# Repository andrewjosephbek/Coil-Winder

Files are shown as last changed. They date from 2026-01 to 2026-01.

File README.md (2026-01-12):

# Coil Winder

A **low-cost, precision coil winding machine** built from 3D-printed parts and off-the-shelf components, designed for sensing coils, charging coils, solenoids, and similar applications. See detailed system descriptions and methodology in **Design Docs**. 




---

## Highlights
- Winds coils up to **30 mm length × 250 mm diameter**
- Single-piece **3D-printed frame** for tight tolerances and fast assembly
- **Arbor + Eye architecture** for accurate wire placement
- **Stepper-driven arbor** with 3:1 belt reduction for consistent tension
- **Worm-gear driven eye (40:1)** for fine linear positioning
- Custom **4-layer driver PCB** (STM32L432 + DRV8825)
- **FreeRTOS-based firmware** with prioritized motor control and UI tasking

---

## System Overview
- **Arbor Assembly:** Rotates the coil form and maintains wire tension  
- **Eye Assembly:** Precisely guides wire placement across the arbor  
- **Driver Board:** Handles UI, motor drivers, and peripherals  

---

## Tech Stack
STM32L432 · DRV8825 · FreeRTOS · Step/Dir Steppers · 4-layer PCB · 3D Printing

---

## Capabilities
- Tightly packed first-layer winding
- Supports **30 AWG wire**
- Integrated button-based user interface

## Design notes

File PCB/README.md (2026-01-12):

# coilwinder PCB

[Replace these texts and sections as needed.  This file should desribe the PCB, and associated information.]

## Background

[Fill this out with general info]

## [Next Section]

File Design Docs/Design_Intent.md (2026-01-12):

# Design Intent

This document is a high level overview of the design and structure of this project.

## Project Structure

This project intends to provide a simple and cost effective way to wind coils, using 3D printed and off the shelf components. It's maximum coil size of 30mm Lg x ⌀250mm makes this project well suited for sensing coils, charging coils, solenoids, and similar applications. At the highest possible level, this project is split into two mechanical assemblies, and one electrical assembly. These assemblies are described below:

- The Arbor is the form on which the coil is wound. It's driven by the *Arbor Motor Assembly*.
- The Eye sets the position of the wire relative to the arbor. It's driven by the *Eye Motor Assembly*.
- The *Driver Board* manages and controls the user interface, motors, and other peripherals.

## Mechanical Component Structure

The mechanical side of this project is built on a single part, 3D printed frame. By printing the frame as a single part, tight position tolerances can be met without the need for measuring and positioning components by hand. It also saves on assembly time. 

### Arbor Motor Assembly

The Arbor Motor Assembly is comprised mainly of a stepper motor with a 3:1 timing pulley gear reduction. This provides the necessary torque to maintain tension on the wire while the coil is wound. The Arbor itself is 3D printed and parametric, so that it may be scaled to accommodate a variety of coil sizes. It includes a wire retention screw to keep the wire tight wile the first coil is being wound, as well as coil tie off slots that allow the user to mechanically support the coil before it's removed from the Arbor.

### Eye Motor Assembly

The Eye Motor Assembly uses a 40:1 worm gear reduction to accurately position the eye relative to the Arbor. When the coil winding process starts, the Eye first finds an initial reference angle using a limit switch. It uses this reference angle alongside some computation to determine it's linear position from it's angular position. This method of extracting linear motion from angular motion was chosen since it provides very fine positional resolution and uses fewer parts then a traditional linear rail and lead screw system.

## Control Flow

This project is divided into two tasks (or "threads"), with control flow managed via FreeRTOS. The UI Task (which manages the User Interface) is of Normal OS priority. When the user begins the coil winding process, the UI Task Resumes the execution of the Motor Task. Since the Motor Task is of Above Average OS priority, it takes priority in execution, and only relinquishes control once the coil winder process concludes. This is done intentionally, as an extended interruption in execution may cause the arbor to lose tension on the wire being would, creating a defect in the coil. The UI and Motor Tasks are described below:

### UI Task

The UI task receives user input and updates the User Interface accordingly. The UI Task manages manages the followings sup-processes in the order described below.

#### Setup

1. Initializes the display where the UI is printed
2. Prints the user interface

#### Loop

1. Polls input from the user
2. Set's the position of the user's cursor
3. Updates the value (stored in memory) of the field the user is currently editing
4. Updates the value of the field displayed on the screen from the value stored in memory
5. Chooses to allows the Motor Task to begin execution.

### Motor Task

The Motor Task operates the coil winding process. The Motor Task manages manages the followings sub-processes in the order described below.

#### Setup
1. Initializes and enables stepper motor drivers
2. Suspends the Motor Task

#### Loop
1. Guides the user through the coil winding process through on screen prompts
2. Calculates the required steps to move the Eye at distances specified during the UI Task, and executes those steps. Calculates the required delay to move the Arbor at a consistent speed with respect to it's diameter, and executes those steps
3. Sleeps and disables the stepper motor drivers
4. Reminds the UI Task to redraw it's UI when the coil winding process has concluded
5. Suspends the Motor Task

## Code Structure

The two main tasks call a set of libraries that keep the data they manage organized and the code they run on dry. Each library defines an object that stores data about the component the library is meant to represent. These libraries and their interactions are described in the flow chart and object descriptions below:

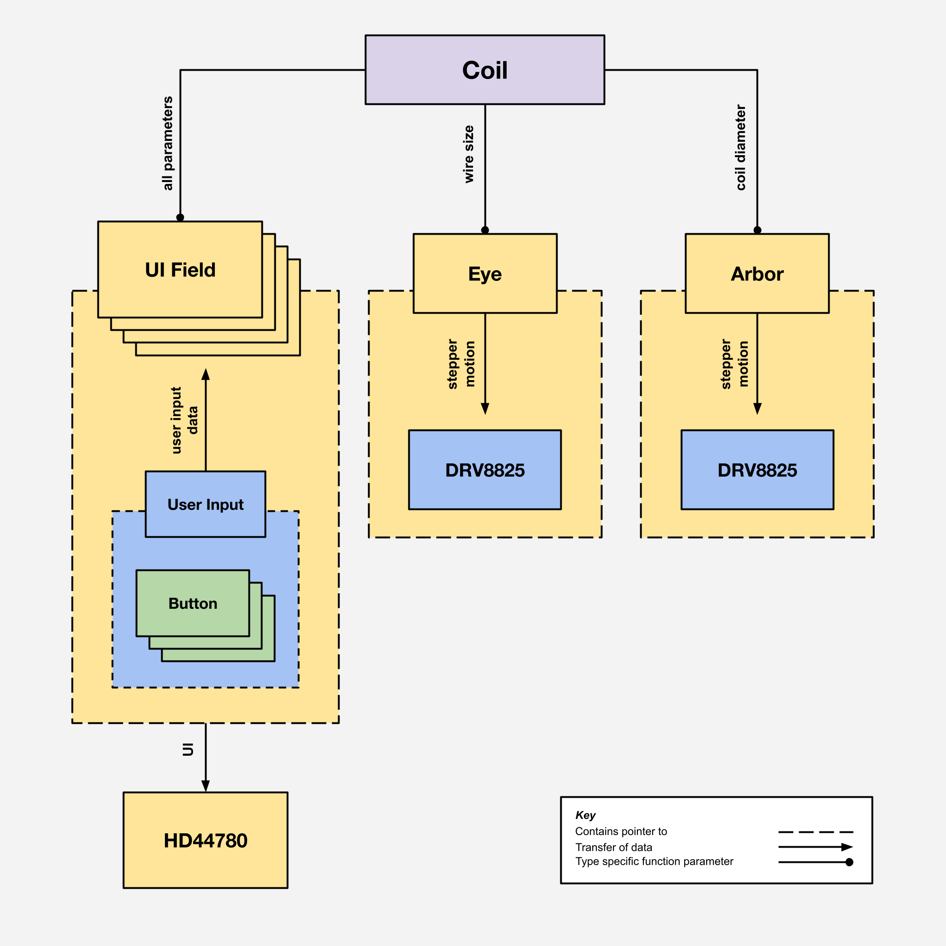
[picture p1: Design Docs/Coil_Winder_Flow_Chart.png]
Flow Chart Title


- `CoilParameters_t` an object that stores the dimensions of the coil to be wound. It's corresponding library can be used to access and change these dimensions.
- `Button_t` an object that stores the GPIO interface and state of a button. This information is used in the Button object's corresponding library to support features like customizable press and hold behaviors, as well as normally open and normally closed switch types.
- `ArborParameters_t` an object that stores the Arbors surface speed and a pointer to it's corresponding . It's corresponding library can be used to rotate the Arbor, and set it's surface speed automatically based on the size of the coil being used.
- `DRV8825_Stepper_t` an object that stores GPIO information about a DRV8825_Stepper_t stepper driver chip. IIt's corresponding library provides low level control of most of the chips functions. 
- `EyeParameters_t` an object that stores the position, length, and DRV8825_Stepper_t for the Eye. It's corresponding library can be used to find it's home position or move the a predetermined distance 
- `UserInput_t` an object that can be used to retrieve user input as a single 32 bit value. It polls it's associated Button_t objects and aggregates their outputs into a single enumeration.
    - It's important to poll user input *only once per tick*. Otherwise, some statements executed in the same tick may see different user input values.
- `UIField_t` an object that stores the title and data accessor functions for a UI field. It's corresponding library can be used to print and update the UI field.

## Driver Board Component Choices

The Driver Board is a 4 layer PCB that serves to drive the display and stepper motors. The components utilized and justifications for their usage are described below.

- The ***STM32L432KCU6*** was chosen as this projects MCU for it's low cost, low power draw, and appropriate number of GPIO ports. 
- The ***DRV8825*** was chosen to drive this projects stepper motors for it's simple step and direction interface. It's current setting potentiometer also negates the need for a SPI current setting and interface, which saves on the number of required MCU GPIO ports.
- The ***AZ1117C*** was chosen for LCD and MCU voltage regulation, as it comes preset at 5V and 3.3V levels, which lowers the number of supporting components required on the PCB.

All other components are standard/trivial supporting components chosen for easy hand-soldering assembly. All SMD resistors and capacitors are package size 0603 (Imperial).

## Current Issues

Though this project currently works as intended, some issues must be addresses before it is developed further:

- Motor task currently performs some limited display functions
    - Would require Motor Task to relinquish control during execution, and for more data to be shared between tasks
- GPIO ports won't Read/Write without first being driven from incorrect port on line 615.

## Planned Updates

In it's current state, this project is in the process of transitioning from working prototype and a first product iteration. In the future, I hope to:

- Transition to a 2 layer PCB, to save on cost
- Design an enclosure to house the display and driver electronics
- Transition to USB as the projects primary power source

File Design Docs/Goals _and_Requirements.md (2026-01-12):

# Goals and Requirements

Requirements describe features that must be implemented, goals are features that may be added once a minimum viable product is achieved.

## Requirements

- Wind coils with a minimum diameter of 25cm
- Reliably wind a tightly packed first wire layer 
    - e.g. minimal space between wraps
- Accomplish all previous requirements with a minimum wire size of 30awg 
- Operate the Coil Winder through an integrated user interface 

## Goals

- Design a system to ensure non initial layers are tightly packed
    - e.g. successive layers are wrapped within the root of previous layers
- Design an arbor standard with space for a time of flight (ToF) sensor to read the radius of the Arbor at the current winding position
    - Use sensor data to adjust arbor speed, and automatically read arbor radius.
- Wind coils with a minimum diameter of 50cm
- Accomplish all previous goals with a minimum wire size of 32awg

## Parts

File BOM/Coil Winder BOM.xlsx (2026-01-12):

Country of Origin may be different at time of shipment.
The HTSUS and ECCN information shown is for informational purposes only and is not a representation or warranty as to the accuracy or reliability of these classifications. All information is provided "as is" and is subject to change without notice. Any use made of the information provided is without recourse to Digi-Key and at the user's risk.
Index | Manufacturer Part Number | Manufacturer Name | Description | Lead Time | Availability | Stock Status | Attrition % | Requested Quantity 1 | Pack Quantity 1 | Pack Type 1 | Digi-Key Part Number 1 | Unit Price 1 | Extended Price 1 | Minimum Order Quantity 1 | Customer Reference | Requested Part Number | Lead Weeks | Datasheet | Reference Designator | US Import Tariff | Note | Part Status | RoHS Status | REACH Status | Moisture Sensitivity Level (MSL) | ECCN | HTSUS | Country of Origin | Environmental Information | Original Part numbers | Image | Product Notes
1 | CL10A106MQ8NNNC | Samsung Electro-Mechanics | CAP CER 10UF 6.3V X5R 0603 |  | 907,339 | In Stock |  | 2 | 2 | Cut Tape (CT) | 1276-1119-1-ND | 0.08000 | $0.16 | 1 |  | 1276-1119-1-ND | 31 | https://mm.digikey.com/Volume0/opasdata/d220001/medias/docus/609/CL10A106MQ8NNNC_Spec.pdf |  | N/A |  | Active | ROHS3 Compliant | REACH Unaffected | 1 (Unlimited) | EAR99 | 8532.24.0020 | Philippines | https://www.samsungsem.com/files/fileDown.do?key=ed1dfdfa-645e-4252-b707-17f9b1502dd1|https://www.samsungsem.com/global/support/certificate/product-stewardship.do | 1276-1119-1-ND | https://mm.digikey.com/Volume0/opasdata/d220001/medias/images/2537/Ceramic-Capacitor-CL-Series.jpg
2 | CL10A226MP8NUNE | Samsung Electro-Mechanics | CAP CER 22UF 10V X5R 0603 |  | 3,690,429 | In Stock |  | 2 | 2 | Cut Tape (CT) | 1276-1274-1-ND | 0.08000 | $0.16 | 1 |  | 1276-1274-1-ND | 31 | https://mm.digikey.com/Volume0/opasdata/d220001/medias/docus/2901/CL10A226MP8NUNC_Spec.pdf |  | N/A |  | Active | ROHS3 Compliant | REACH Unaffected | 1 (Unlimited) | EAR99 | 8532.24.0020 | Philippines | https://www.samsungsem.com/files/fileDown.do?key=ed1dfdfa-645e-4252-b707-17f9b1502dd1|https://www.samsungsem.com/global/support/certificate/product-stewardship.do | 1276-1274-1-ND | https://mm.digikey.com/Volume0/opasdata/d220001/medias/images/2537/Ceramic-Capacitor-CL-Series.jpg
3 | CL10B103KB8NNNC | Samsung Electro-Mechanics | CAP CER 10000PF 50V X7R 0603 |  | 2,744,577 | In Stock |  | 1 | 1 | Cut Tape (CT) | 1276-1009-1-ND | 0.08000 | $0.08 | 1 |  | 1276-1009-1-ND | 31 | https://mm.digikey.com/Volume0/opasdata/d220001/medias/docus/609/CL10B103KB8NNNC_Spec.pdf |  | May apply on shipments to the U.S. |  | Active | ROHS3 Compliant | REACH Unaffected | 1 (Unlimited) | EAR99 | 8532.24.0020 | China | https://www.samsungsem.com/files/fileDown.do?key=ed1dfdfa-645e-4252-b707-17f9b1502dd1|https://www.samsungsem.com/global/support/certificate/product-stewardship.do | 1276-1009-1-ND | https://mm.digikey.com/Volume0/opasdata/d220001/medias/images/2537/Ceramic-Capacitor-CL-Series.jpg
4 | CL10B104KB8NNNC | Samsung Electro-Mechanics | CAP CER 0.1UF 50V X7R 0603 |  | 1,071,440 | In Stock |  | 11 | 11 | Cut Tape (CT) | 1276-1000-1-ND | 0.03500 | $0.39 | 1 |  | 1276-1000-1-ND | 31 | https://mm.digikey.com/Volume0/opasdata/d220001/medias/docus/609/CL10B104KB8NNNC_Spec.pdf |  | N/A |  | Active | ROHS3 Compliant | REACH Unaffected | 1 (Unlimited) | EAR99 | 8532.24.0020 | Philippines | https://www.samsungsem.com/files/fileDown.do?key=ed1dfdfa-645e-4252-b707-17f9b1502dd1|https://www.samsungsem.com/global/support/certificate/product-stewardship.do | 1276-1000-1-ND | https://mm.digikey.com/Volume0/opasdata/d220001/medias/images/2537/Ceramic-Capacitor-CL-Series.jpg
5 | CL10A105KA8NNNC | Samsung Electro-Mechanics | CAP CER 1UF 25V X5R 0603 |  | 211,665 | In Stock |  | 1 | 1 | Cut Tape (CT) | 1276-1102-1-ND | 0.08000 | $0.08 | 1 |  | 1276-1102-1-ND | 31 | https://mm.digikey.com/Volume0/opasdata/d220001/medias/docus/609/CL10A105KA8NNNC_Spec.pdf |  | N/A |  | Active | ROHS3 Compliant | REACH Unaffected | 1 (Unlimited) | EAR99 | 8532.24.0020 | Philippines | https://www.samsungsem.com/files/fileDown.do?key=ed1dfdfa-645e-4252-b707-17f9b1502dd1|https://www.samsungsem.com/global/support/certificate/product-stewardship.do | 1276-1102-1-ND | https://mm.digikey.com/Volume0/opasdata/d220001/medias/images/2537/Ceramic-Capacitor-CL-Series.jpg
6 | CL10A475KQ8NNNC | Samsung Electro-Mechanics | CAP CER 4.7UF 6.3V X5R 0603 |  | 920,375 | In Stock |  | 2 | 2 | Cut Tape (CT) | 1276-1045-1-ND | 0.08000 | $0.16 | 1 |  | 1276-1045-1-ND | 31 | https://mm.digikey.com/Volume0/opasdata/d220001/medias/docus/609/CL10A475KQ8NNNC_Spec.pdf |  | N/A |  | Active | ROHS3 Compliant | REACH Unaffected | 1 (Unlimited) | EAR99 | 8532.24.0020 | Philippines | https://www.samsungsem.com/files/fileDown.do?key=ed1dfdfa-645e-4252-b707-17f9b1502dd1|https://www.samsungsem.com/global/support/certificate/product-stewardship.do | 1276-1045-1-ND | https://mm.digikey.com/Volume0/opasdata/d220001/medias/images/2537/Ceramic-Capacitor-CL-Series.jpg
7 | CGA3E1X7R1V474K080AC | TDK Corporation | CAP CER 0.47UF 35V X7R 0603 |  | 121,365 | In Stock |  | 2 | 2 | Cut Tape (CT) | 445-6928-1-ND | 0.22000 | $0.44 | 1 |  | 445-6928-1-ND | 12 | https://product.tdk.com/system/files/dam/doc/product/capacitor/ceramic/mlcc/catalog/mlcc_automotive_general_en.pdf |  | N/A |  | Active | ROHS3 Compliant | REACH Unaffected | 1 (Unlimited) | EAR99 | 8532.24.0020 | Japan | https://product.tdk.com/system/files/dam/doc/product/capacitor/ceramic/mlcc/rohs/mlccrohs_automotive_general_en.pdf|https://product.tdk.com/en/environment/index.html | 445-6928-1-ND | https://mm.digikey.com/Volume0/opasdata/d220001/medias/images/2097/CGA-Series-0603-%281608-Metric%29.jpg
8 | ESK107M025AE3EA | KEMET | CAP ALUM 100UF 20% 25V RADIAL TH |  | 73,926 | In Stock |  | 2 | 2 | Cut Tape (CT) | 399-6650-1-ND | 0.20000 | $0.40 | 1 |  | 399-6650-1-ND | 17 | https://www.yageogroup.com/content/datasheet/asset/file/KEM_A4004_ESK |  | May apply on shipments to the U.S. |  | Active | ROHS3 Compliant | REACH Unaffected | Not Applicable | EAR99 | 8532.22.0020 | China |  | 399-6650-1-ND | https://mm.digikey.com/Volume0/opasdata/d220001/medias/images/630/ESK107M035AE3AA.JPG
9 | RMCF0201FT49K9 | Stackpole Electronics Inc | RES 49.9K OHM 1% 1/20W 0201 |  | 86,860 | In Stock |  | 2 | 2 | Cut Tape (CT) | RMCF0201FT49K9CT-ND | 0.10000 | $0.20 | 1 |  | RMCF0201FT49K9CT-ND | 18 | https://www.seielect.com/catalog/SEI-RMCF_RMCP.pdf |  | N/A |  | Active | ROHS3 Compliant | REACH Unaffected | 1 (Unlimited) | EAR99 | 8533.21.0030 | Taiwan | https://www.seielect.com/catalog/SEI-RoHS_Compliance_Status.pdf|https://www.seielect.com/catalog/reach.pdf|https://www.seielect.com/catalog/sei-coc%20prop%2065.pdf | RMCF0201FT49K9CT-ND | https://mm.digikey.com/Volume0/opasdata/d220001/medias/images/4850/738_0201-RMCF-Series.jpg
10 | RMCF0201FT30K0 | Stackpole Electronics Inc | RES 30K OHM 1% 1/20W 0201 |  | 9,301 | In Stock |  | 2 | 2 | Cut Tape (CT) | RMCF0201FT30K0CT-ND | 0.10000 | $0.20 | 1 |  | RMCF0201FT30K0CT-ND | 18 | https://www.seielect.com/catalog/SEI-RMCF_RMCP.pdf |  | N/A |  | Active | ROHS3 Compliant | REACH Unaffected | 1 (Unlimited) | EAR99 | 8533.21.0030 | Taiwan | https://www.seielect.com/catalog/SEI-RoHS_Compliance_Status.pdf|https://www.seielect.com/catalog/reach.pdf|https://www.seielect.com/catalog/sei-coc%20prop%2065.pdf | RMCF0201FT30K0CT-ND | https://mm.digikey.com/Volume0/opasdata/d220001/medias/images/4850/738_0201-RMCF-Series.jpg
11 | UCR006YVPFLR200 | Rohm Semiconductor | RES 0.2 OHM 1% 1/10W 0201 |  | 23,752 | In Stock |  | 4 | 4 | Cut Tape (CT) | RHM1701-1-ND | 0.56000 | $2.24 | 1 |  | RHM1701-1-ND | 8 | https://fscdn.rohm.com/en/products/databook/datasheet/passive/resistor/chip_resistor/ucr-e.pdf |  | N/A |  | Active | ROHS3 Compliant | REACH Unaffected | 1 (Unlimited) | EAR99 | 8533.21.0030 | Thailand |  | RHM1701-1-ND | https://mm.digikey.com/Volume0/opasdata/d220001/medias/images/5652/511_UCR03.jpg
12 | RMCF0201FT10K0 | Stackpole Electronics Inc | RES 10K OHM 1% 1/20W 0201 |  |  | In Stock |  | 2 | 2 | Cut Tape (CT) | RMCF0201FT10K0CT-ND | 0.10000 | $0.20 | 1 |  | RMCF0201FT10K0CT-ND | 18 | https://www.seielect.com/catalog/SEI-RMCF_RMCP.pdf |  | N/A |  | Active | ROHS3 Compliant | REACH Unaffected | 1 (Unlimited) | EAR99 | 8533.21.0030 | Taiwan | https://www.seielect.com/catalog/SEI-RoHS_Compliance_Status.pdf|https://www.seielect.com/catalog/reach.pdf|https://www.seielect.com/catalog/sei-coc%20prop%2065.pdf | RMCF0201FT10K0CT-ND | https://mm.digikey.com/Volume0/opasdata/d220001/medias/images/4322/cut-tape-render.jpg
13 | CRCW02011M00FKED | Vishay Dale | RES SMD 1M OHM 1% 1/20W 0201 |  | 95,279 | In Stock |  | 2 | 2 | Cut Tape (CT) | 541-1.00MAABCT-ND | 0.21000 | $0.42 | 1 |  | 541-1.00MAABCT-ND | 18 | https://www.vishay.com/docs/20052/crcw0201e3.pdf |  | N/A |  | Active | ROHS3 Compliant | REACH Unaffected | 1 (Unlimited) | EAR99 | 8533.21.0030 | Malaysia |  | 541-1.00MAABCT-ND | https://mm.digikey.com/Volume0/opasdata/d220001/medias/images/596/Vishay-CRCW-0201.jpg
14 | 694108106102 | Würth Elektronik | CONN PWR JACK 2.5X5.5MM SOLDER |  | 3,450 | In Stock |  | 1 | 1 | Cut Tape (CT) | 732-5933-1-ND | 1.80000 | $1.80 | 1 |  | 732-5933-1-ND | 13 | https://www.we-online.com/components/products/datasheet/694108106102.pdf |  | May apply on shipments to the U.S. |  | Active | ROHS3 Compliant | REACH Unaffected | Not Applicable | EAR99 | 8536.69.4010 | China | https://mm.digikey.com/Volume0/opasdata/d220001/medias/docus/744/Certificate_of_Compliance_ROHS.pdf | 732-5933-1-ND | https://mm.digikey.com/Volume0/opasdata/d220001/medias/images/864/MFG_69410x106102.jpg
15 | 694106106102 | Würth Elektronik | CONN PWR JACK 2.05X5.5MM SOLDER |  | 7,580 | In Stock |  | 1 | 1 | Cut Tape (CT) | 732-5929-1-ND | 1.80000 | $1.80 | 1 |  | 732-5929-1-ND | 13 | https://www.we-online.com/components/products/datasheet/694106106102.pdf |  | May apply on shipments to the U.S. |  | Active | ROHS3 Compliant | REACH Unaffected | Not Applicable | EAR99 | 8536.69.4010 | China | https://mm.digikey.com/Volume0/opasdata/d220001/medias/docus/744/Certificate_of_Compliance_ROHS.pdf | 732-5929-1-ND | https://mm.digikey.com/Volume0/opasdata/d220001/medias/images/864/MFG_69410x106102.jpg
16 | TL1150AF070Q | E-Switch | SWITCH TACTILE SPST-NO 0.05A 30V |  | 178,649 | In Stock |  | 1 | 1 | Bulk | EG4414-ND | 0.64000 | $0.64 | 1 |  | EG4414-ND | 15 | https://configured-product-images.s3.amazonaws.com/Datasheets/TL1150.pdf |  | May apply on shipments to the U.S. |  | Active | ROHS3 Compliant | REACH Unaffected | 1 (Unlimited) | EAR99 | 8536.50.9031 | China | http://rohs.e-switch.com/rohs/Series_TL1150_Cert_revA_.pdf|https://sten-eswitch-13110800-production.s3.amazonaws.com/system/asset/document/274/original/RoHS.pdf | EG4414-ND | https://mm.digikey.com/Volume0/opasdata/d220001/medias/images/906/MFG_TL1150AF070Q.jpg
17 | 16ZLH100MEFC5X11 | Rubycon | CAP ALUM 100UF 20% 16V RADIAL TH |  | 112,169 | In Stock |  | 1 | 1 | Bulk | 1189-1148-ND | 0.23000 | $0.23 | 1 |  | 1189-1148-ND | 21 | https://www.rubycon.co.jp/wp-content/uploads/catalog-aluminum/ZLH.pdf |  | N/A |  | Active | ROHS3 Compliant | REACH Unaffected | Not Applicable | EAR99 | 8532.22.0020 | Indonesia |  | 1189-1148-ND | https://mm.digikey.com/Volume0/opasdata/d220001/medias/images/524/16ZLH100MEFC5X11.JPG

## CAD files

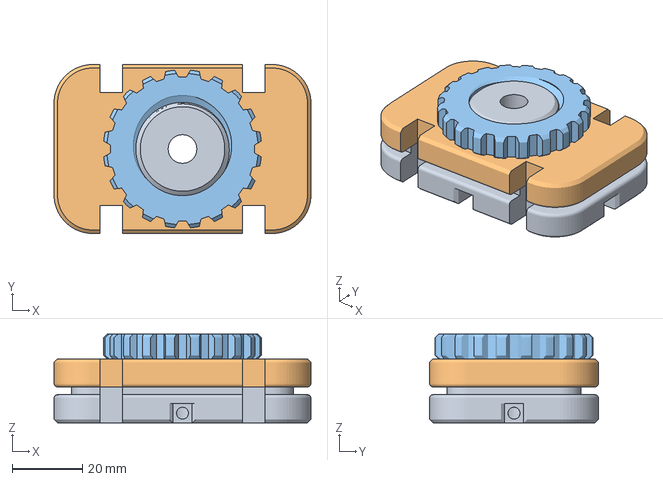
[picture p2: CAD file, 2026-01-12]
Printable Parts/3 Part Rectangular Arbor v4.3mf
73.0 x 48.0 x 25.2 mm

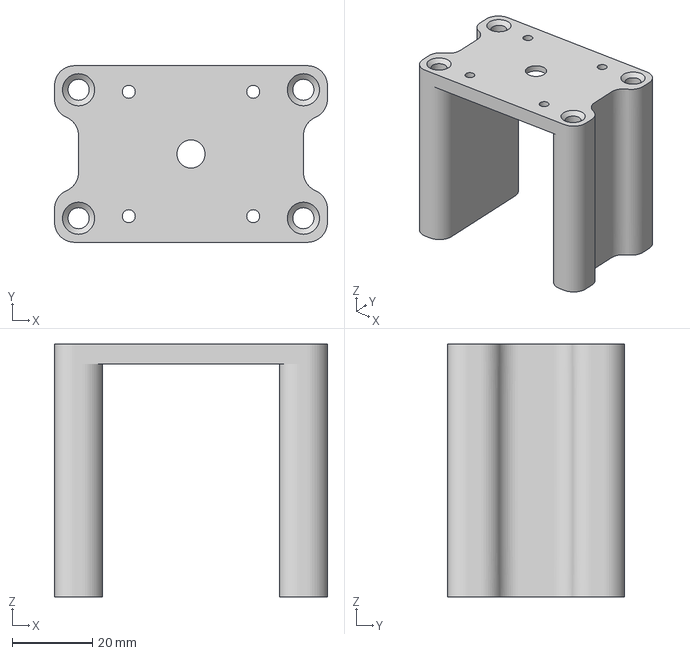
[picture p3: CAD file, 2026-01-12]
Printable Parts/Worm Motor Mount v10.3mf
68.0 x 44.0 x 63.0 mm

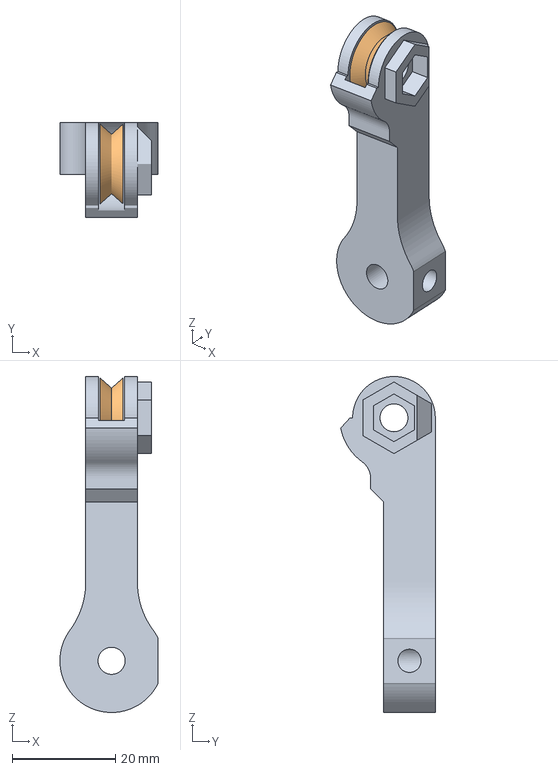
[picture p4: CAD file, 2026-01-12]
Printable Parts/Updated Eye v4.3mf
19.0 x 18.3 x 65.0 mm

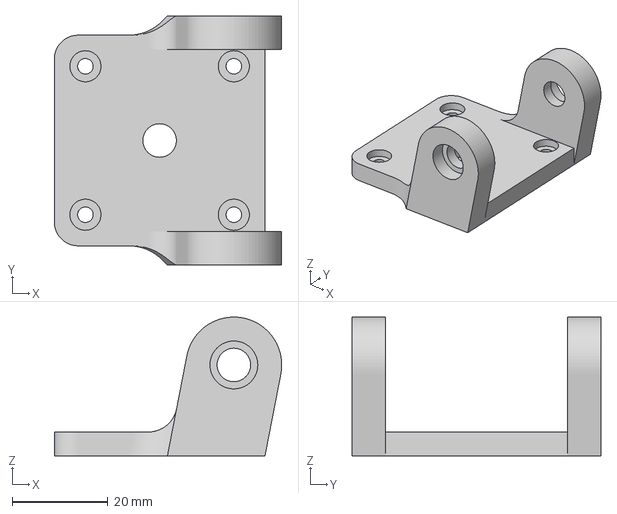
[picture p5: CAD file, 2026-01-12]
Printable Parts/Worm Mount v11.3mf
47.5 x 52.0 x 29.0 mm

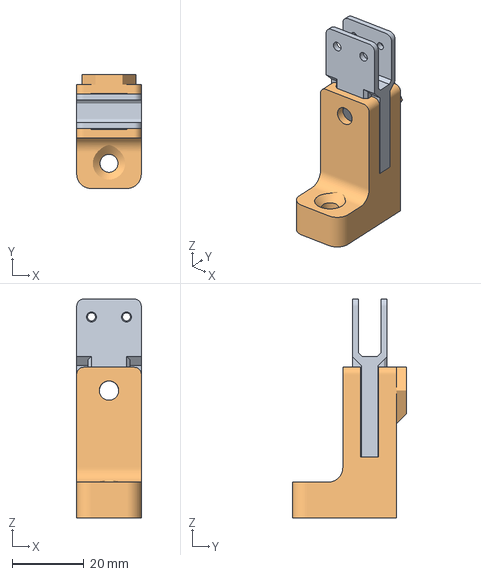
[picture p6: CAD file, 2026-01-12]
Printable Parts/Limit Switch Holder Adjustable v1.3mf
18.0 x 31.8 x 61.0 mm

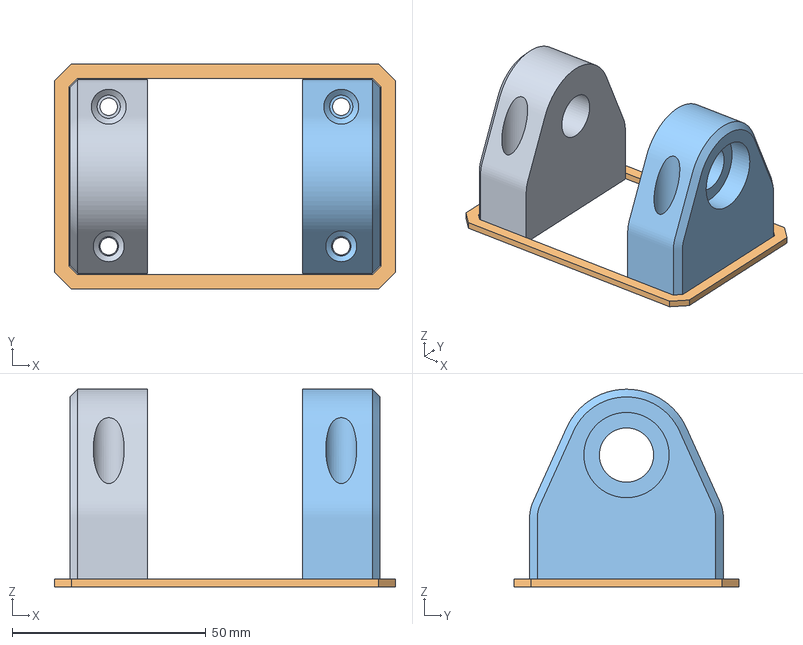
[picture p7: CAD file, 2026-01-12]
Printable Parts/Pillow Blocks v4.3mf
88.0 x 58.0 x 51.0 mm

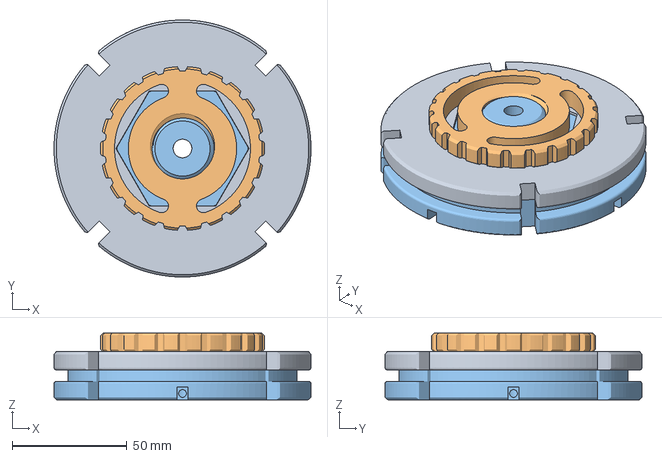
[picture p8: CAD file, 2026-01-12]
Printable Parts/3 Part Round Arbor v2.3mf
112.0 x 112.0 x 29.0 mm

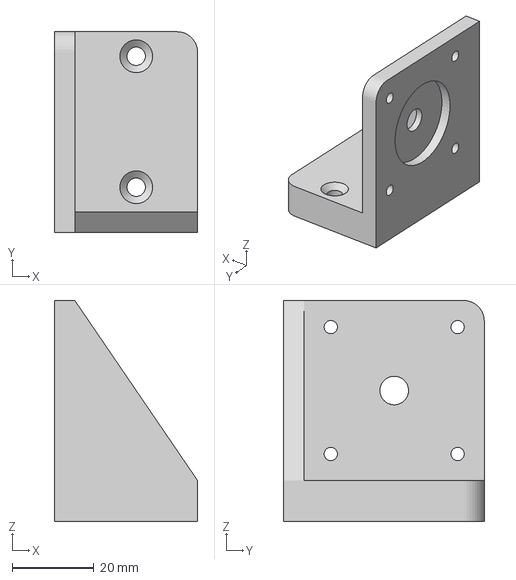
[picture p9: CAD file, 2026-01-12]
Printable Parts/Stepper Pulley Mount v4.3mf
35.0 x 49.0 x 54.0 mm

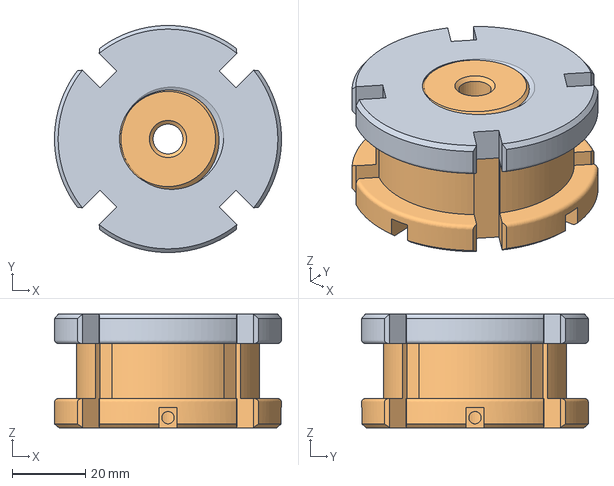
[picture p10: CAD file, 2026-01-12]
Printable Parts/2 Part Round Arbor v10.3mf
62.0 x 62.0 x 31.0 mm

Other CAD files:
Printable Parts/2 Part Round Arbor v11.f3d
Printable Parts/3 Part Rectangular Arbor v4.f3d
Printable Parts/3 Part Round Arbor v2.f3d

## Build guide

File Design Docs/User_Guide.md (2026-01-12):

# User Guide

This document provides steps and recommendations to get this project up and running

## Overview 

This project intends to provide a simple way of winding wire coils. It's composed of a few main assemblies:

- The *Frame* is a single printed part that contains the  *Arbor* and *Eye* assemblies

    - The *Arbor* is the form on which the coil is wound
    - The *Arbor Motor Assembly* contains the *Arbor* and components used to rotate it
    - The *Eye* sets the position of the wire relative to the arbor
    - The *Eye Motor Assembly* contains the *Eye* and components used to drive it's position

## Assembly Instructions  

### Parts List

| Part | Qty |
|:--- |:---:|
| Ball Bearing (22mm OD, 8mm ID, 7mm Wd) | 2 |
| Ball Bearing (10mm OD, 5mm ID, 4mm Wd) | 3 |
| Shaft Collar (5mm ID) | 1 |
| Shaft Collar (8mm ID) | 2 |
| Worm Wheel (Module 0.5) | 1 |
| Worm Gear (Module 0.5) | 1 |
| 4 wire NEMA 17 Stepper Motor (48mm Lg) | 2 |
| M2 x 10mm Screw | 2 |
| M3 x 10mm Screw | 9 |
| M5 x 12mm Screw | 2 |
| Shaft (8mm OD, 125mm Lg) | 1 |
| Shaft (5mm OD, 75mm Lg) | 1 |
| Timing Pulley (60T GT2 8mm ID) | 1 |
| Timing Pulley (20T GT2 5mm ID) | 1 |
| Timing Belt (GT2 200mm Lg) | 1 |
| M3 x 10mm Set Screw | 2 |
| M3 Square Nut | 2 |
| M3 Heat Set Insert | 2 |

### Pre-Assembly

Choose an Arbor from the pre-generated list, or create your own with the included .f3d file. Print the Arbor, Eye and Frame, then proceed with the steps below.

### Arbor Motor Assembly

- Install a Stepper Motor on the Arbor Motor Assembly side of the frame using the M3 x 10mm Screws
- Press fit the 22mm OD Ball Bearings into the frame's pillow block assembly 
- Insert the 8mm shaft into the pillow block assembly, sliding on the 60T Pulley and Timing Belt. Secure both sides of the assembly with Shaft Collars (8mm ID).
- Wrap the timing belt around the 20T Timing Pulley, and slide it onto the Arbor Stepper motor shaft
- Press the M3 Square nuts into the Arbor, install the M3 x 10mm Set Screws in the square nuts. 
- Install the heat set insert, and screw on an M3 x 10mm screw. This is the *wire retention screw*.

[comment]: <> (Add images)

### Eye Motor Assembly

- Install a Stepper Motor on the Eye Motor Assembly side of the frame using the M3 x 10mm Screws
- Press fit a 10mm OD Ball Bearing into the printed V-Roller
- Use the M5 x 12mm Screw to capture the V-Roller in the Eye
- Install a heat set insert in the Eye, in the hole perpendicular to the 5mm shaft hole
- Grind a ≈1.5mm x ≈10mm Lg flat onto one end of the 5mm shaft
- Press fit 10mm OD Ball Bearings onto the frame's eye assembly 
- Insert the 5mm shaft into the eye assembly, with the ground end facing the arbor assembly. Do so while sliding on the Worm Wheel as shown. Secure the non-ground end of the assembly with Shaft a Collar (5mm ID)
- Insert the eye onto the open end of the 5mm shaft
- Install the worm on the Eye Stepper motor, allowing the worm wheel to rotate as you do so. Ensure that the Worm and Worm Wheel mesh correctly.
- Use the M2 x 10 mm Screws to install the limit switch

[comment]: <> (Add images)

## User Interface

Three buttons are used to navigate the user interface: 

- The (+) and (-) buttons increase or decrease the values of the field currently selected by the cursor. A long press on either button with rapidly increase or decrease the selected field. 
- The (SELECT) button move the cursor to the next field. The first 4 fields provide information about the coil being wound. 
    - Selecting the arrow field starts the coil winding process when either (+/-) button is pressed. 

## Setup and Usage

Setting up the Arbor correctly is crucial to winding a tight coil. 
- First wind a few centimeters of wire around the wire retention screw and tighten it to secure. Feed the wire through the thin slot inline with the the retention screw. 
- Rest the wire on top of the V-Roller, and install the wire spool on the spool holder.
- Install the Arbor along the Arbor Motor Assembly shaft, leaving the Arbor set screws loose.
- Select the values describing your chosen coil using the user interface, then start the coil winding process.
- Once the Eye has found it's home position, position the Arbor so that the wire is flush with the retention screw wall. Tighten the Arbor set screws to secure.
- Press the select button to begin the coil winding process
- Once the coil has finished winding, remove the Arbor and feed lengths of Lacing/Kapton tape through the 4 rectangular cutouts along the edge of the arbor. Secure the tape around the coil (this will maintain the coil's shape when removed from the Arbor.)
- Remove the coil from the Arbor

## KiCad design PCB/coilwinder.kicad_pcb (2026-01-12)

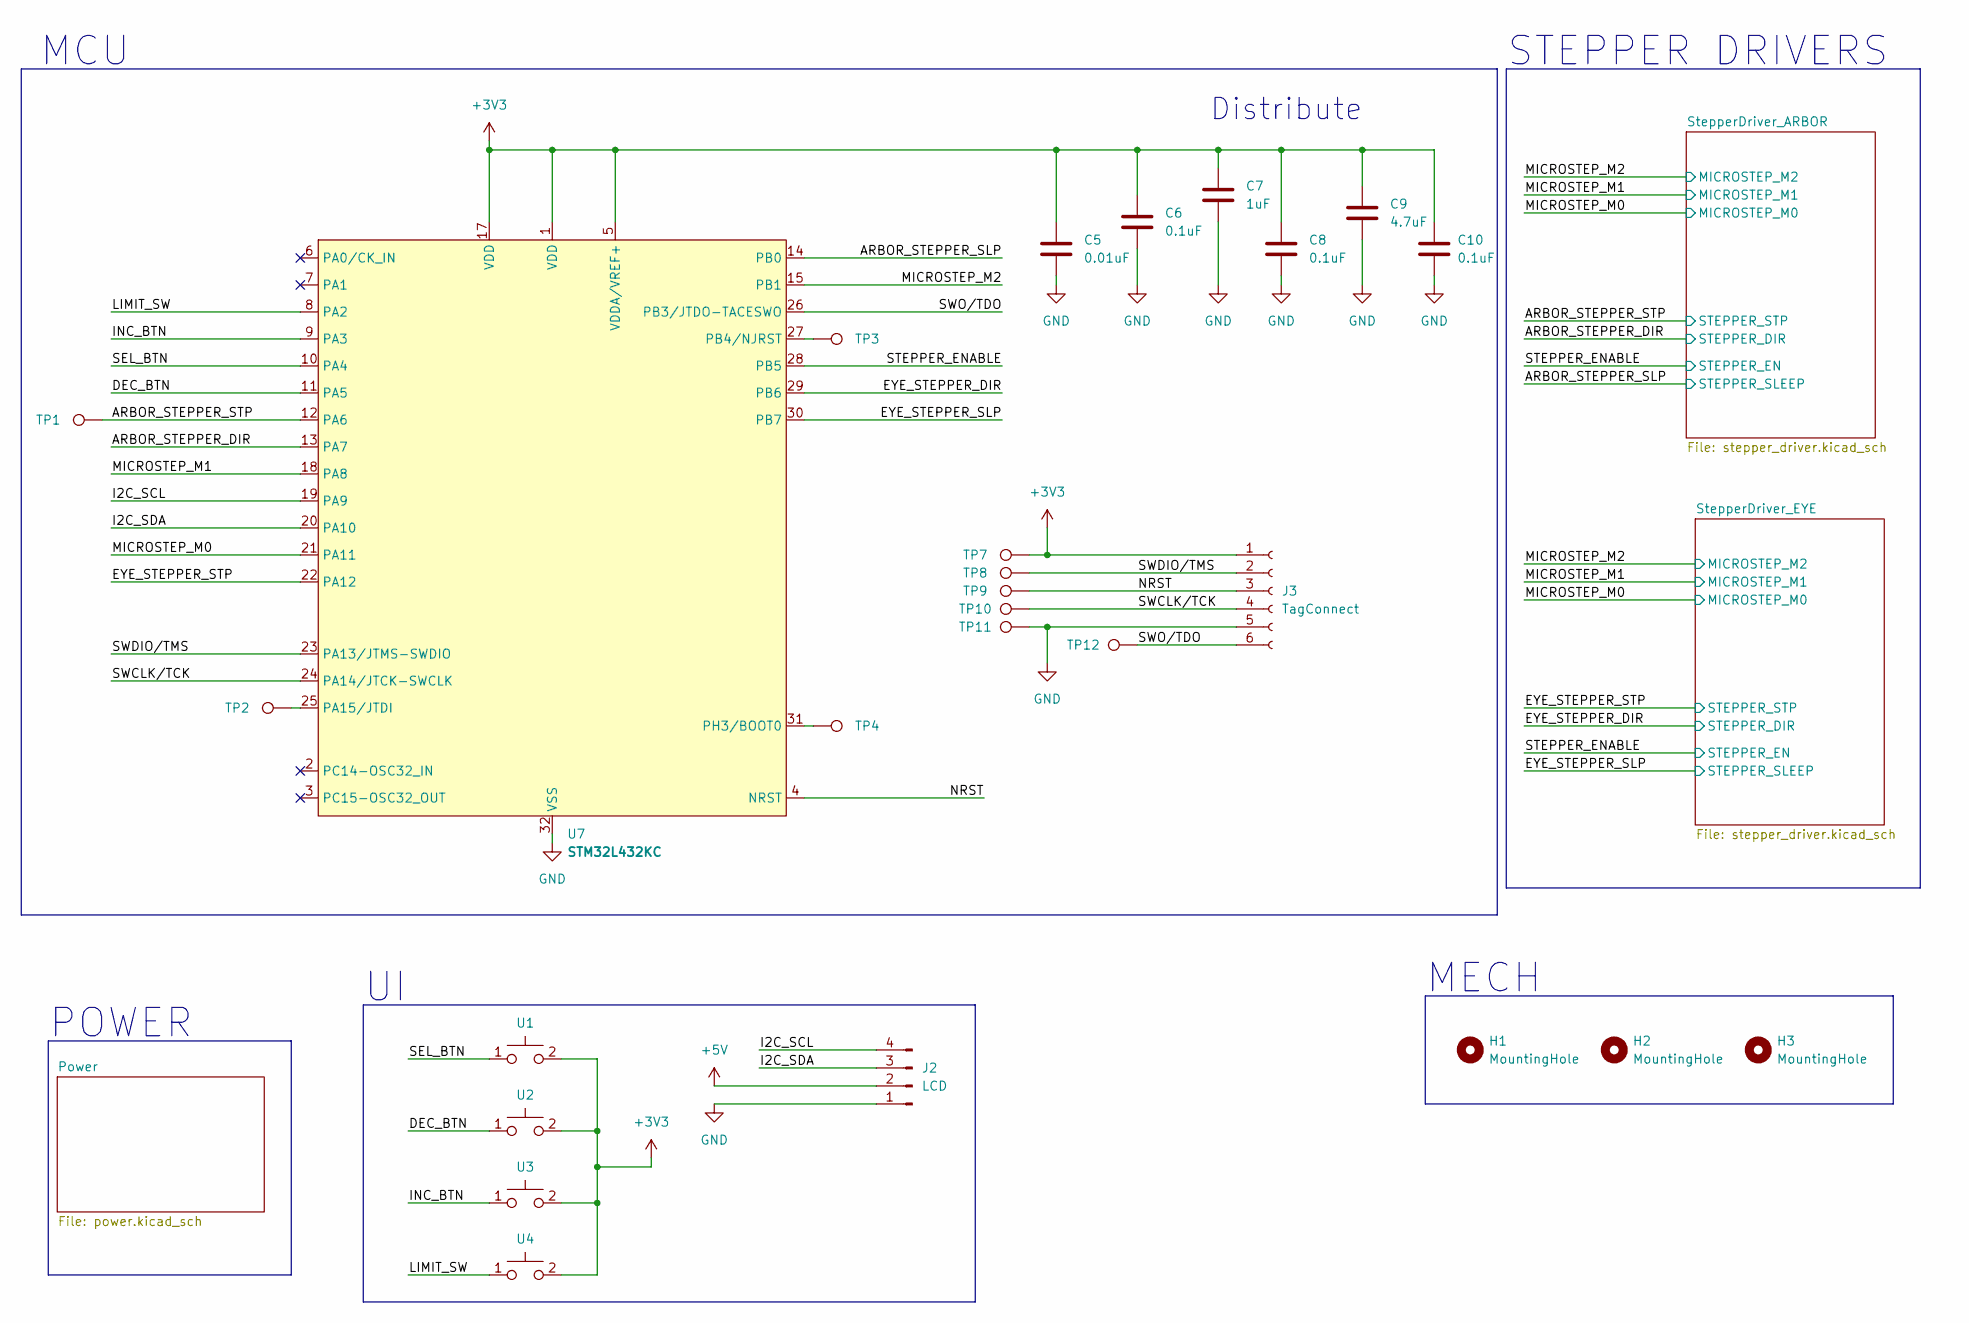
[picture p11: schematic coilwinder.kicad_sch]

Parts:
C5: 0.01uF; C_0603_1608Metric_Pad1.08x0.95mm_HandSolder
C6, C8, C10: 0.1uF; C_0603_1608Metric_Pad1.08x0.95mm_HandSolder
C7: 1uF; C_0603_1608Metric_Pad1.08x0.95mm_HandSolder
C9: 4.7uF; C_0603_1608Metric_Pad1.08x0.95mm_HandSolder
H1, H2, H3: MountingHole; MountingHole_2.2mm_M2
J2: LCD; PinHeader_1x04_P2.54mm_Vertical
J3: TagConnect; Tag-Connect_TC2030-IDC-FP_2x03_P1.27mm_Vertical
TP1: TestPoint; TestPoint_Keystone_5000-5004_Miniature
TP2, TP3, TP4, TP7, TP8, TP9, TP10, TP11, TP12: TestPoint; TestPoint_Pad_1.0x1.0mm
U1, U2, U3: TL1150AF070Q Switch
U4: PinHeader_1x02_P2.54mm_Vertical
U7: STM32L432KC; UFQFPN-32-1EP_5x5mm_P0.5mm_EP3.5x3.5mm

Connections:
+3V3: C5.2, C6.2, C7.2, C8.2, C9.2, C10.2, J3.1, TP7.1, U1.2, U2.2, U3.2, U4.2, U7.1 (VDD), U7.5 (VDDA/VREF+), U7.17 (VDD); also elsewhere on the board
+5V: J2.2; also elsewhere on the board
/ARBOR_STEPPER_DIR: U7.13 (PA7); also elsewhere on the board
/ARBOR_STEPPER_SLP: U7.14 (PB0); also elsewhere on the board
/ARBOR_STEPPER_STP: TP1.1, U7.12 (PA6); also elsewhere on the board
/DEC_BTN: U2.1, U7.11 (PA5)
/EYE_STEPPER_DIR: U7.29 (PB6); also elsewhere on the board
/EYE_STEPPER_SLP: U7.30 (PB7); also elsewhere on the board
/EYE_STEPPER_STP: U7.22 (PA12); also elsewhere on the board
/I2C_SCL: J2.4, U7.19 (PA9)
/I2C_SDA: J2.3, U7.20 (PA10)
/INC_BTN: U3.1, U7.9 (PA3)
/LIMIT_SW: U4.1, U7.8 (PA2)
/MICROSTEP_M0: U7.21 (PA11); also elsewhere on the board
/MICROSTEP_M1: U7.18 (PA8); also elsewhere on the board
/MICROSTEP_M2: U7.15 (PB1); also elsewhere on the board
/NRST: J3.3, TP9.1, U7.4 (NRST)
/SEL_BTN: U1.1, U7.10 (PA4)
/STEPPER_ENABLE: U7.28 (PB5); also elsewhere on the board
/SWCLK/TCK: J3.4, TP10.1, U7.24 (PA14/JTCK-SWCLK)
/SWDIO/TMS: J3.2, TP8.1, U7.23 (PA13/JTMS-SWDIO)
/SWO/TDO: J3.6, TP12.1, U7.26 (PB3/JTDO-TACESWO)
GND: C5.1, C6.1, C7.1, C8.1, C9.1, C10.1, J2.1, J3.5, TP11.1, U7.16 (VSS2), U7.32 (VSS), U7.33 (EXP); also elsewhere on the board
unnamed: TP2.1, U7.25 (PA15/JTDI)
unnamed: TP3.1, U7.27 (PB4/NJRST)
unnamed: TP4.1, U7.31 (PH3/BOOT0)

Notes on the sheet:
Distribute
STEPPER DRIVERS
MECH
MCU
POWER

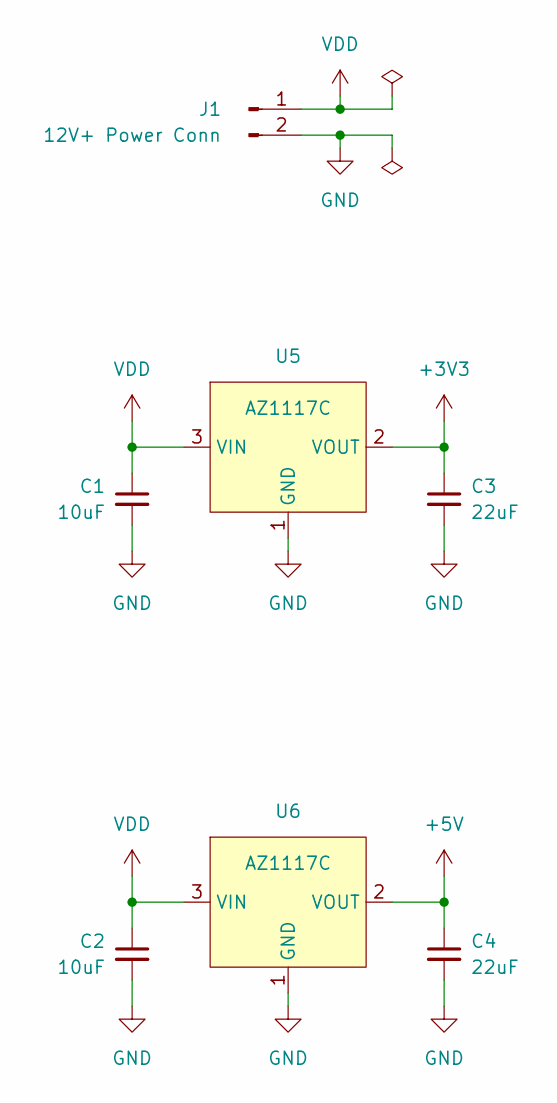
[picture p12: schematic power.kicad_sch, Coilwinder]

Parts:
C1, C2: 10uF; C_0603_1608Metric_Pad1.08x0.95mm_HandSolder
C3, C4: 22uF; C_0603_1608Metric_Pad1.08x0.95mm_HandSolder
J1: 12V+ Power Conn; TerminalBlock_bornier-2_P5.08mm
U5, U6: AZ1117C; SOT-223-3_TabPin2

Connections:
+3V3: C3.1, U5.2 (VOUT); also elsewhere on the board
+5V: C4.1, U6.2 (VOUT2); also elsewhere on the board
GND: C1.2, C2.2, C3.2, C4.2, J1.2, U5.1 (GND), U6.1 (GND); also elsewhere on the board
VDD: C1.1, C2.1, J1.1, U5.3 (VIN), U6.3 (VIN); also elsewhere on the board

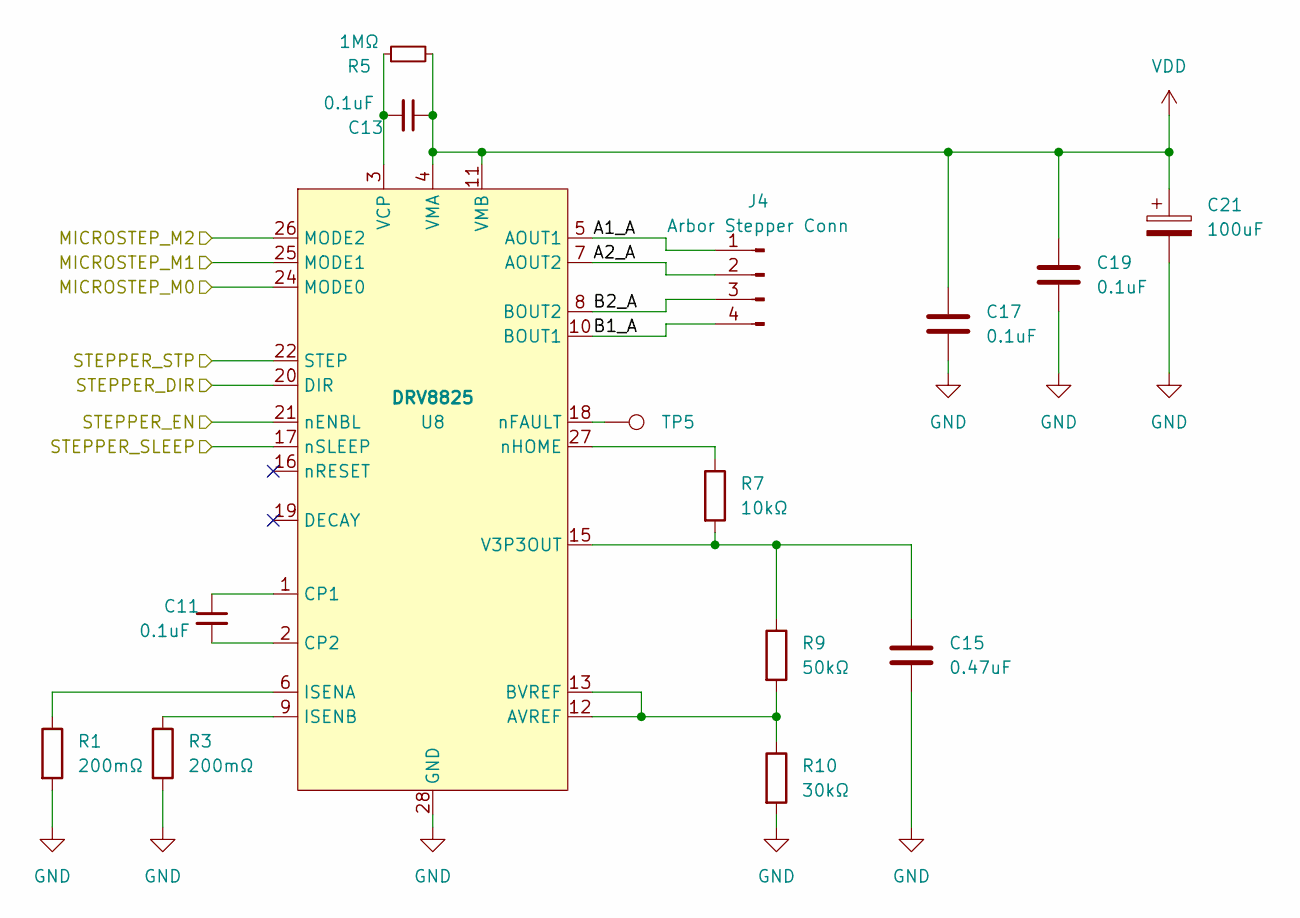
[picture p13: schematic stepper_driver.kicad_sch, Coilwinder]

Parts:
C11, C13, C17, C19: 0.1uF; C_0603_1608Metric_Pad1.08x0.95mm_HandSolder
C15: 0.47uF; C_0603_1608Metric_Pad1.08x0.95mm_HandSolder
C21: 100uF; CP_Radial_D5.0mm_P2.00mm
J4: Arbor Stepper Conn; PinHeader_1x04_P2.54mm_Vertical
R1, R3: 200mΩ; C_0603_1608Metric_Pad1.08x0.95mm_HandSolder
R5: 1MΩ; C_0603_1608Metric_Pad1.08x0.95mm_HandSolder
R7: 10kΩ; C_0603_1608Metric_Pad1.08x0.95mm_HandSolder
R9: 50kΩ; C_0603_1608Metric_Pad1.08x0.95mm_HandSolder
R10: 30kΩ; C_0603_1608Metric_Pad1.08x0.95mm_HandSolder
TP5: TestPoint; TestPoint_Pad_1.0x1.0mm
U8: DRV8825

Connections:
/ARBOR_STEPPER_DIR: U8.20 (DIR); also elsewhere on the board
/ARBOR_STEPPER_SLP: U8.17 (nSLEEP); also elsewhere on the board
/ARBOR_STEPPER_STP: U8.22 (STEP); also elsewhere on the board
/MICROSTEP_M0: U8.24 (MODE0); also elsewhere on the board
/MICROSTEP_M1: U8.25 (MODE1); also elsewhere on the board
/MICROSTEP_M2: U8.26 (MODE2); also elsewhere on the board
/STEPPER_ENABLE: U8.21 (nENBL); also elsewhere on the board
/StepperDriver_ARBOR/A1_A: J4.1, U8.5 (AOUT1)
/StepperDriver_ARBOR/A2_A: J4.2, U8.7 (AOUT2)
/StepperDriver_ARBOR/B1_A: J4.4, U8.10 (BOUT1)
/StepperDriver_ARBOR/B2_A: J4.3, U8.8 (BOUT2)
GND: C15.2, C17.1, C19.1, C21.2, R1.2, R3.2, R10.2, U8.14 (GND2), U8.28 (GND), U8.29 (PPAD); also elsewhere on the board
unnamed: R9.2, R10.1, U8.12 (AVREF), U8.13 (BVREF)
unnamed: C11.1, U8.1 (CP1)
unnamed: C11.2, U8.2 (CP2)
unnamed: R1.1, U8.6 (ISENA)
unnamed: R3.1, U8.9 (ISENB)
unnamed: C15.1, R7.2, R9.1, U8.15 (V3P3OUT)
unnamed: C13.2, R5.1, U8.3 (VCP)
unnamed: TP5.1, U8.18 (nFAULT)
unnamed: R7.1, U8.27 (nHOME)
VDD: C13.1, C17.2, C19.2, C21.1, R5.2, U8.4 (VMA), U8.11 (VMB); also elsewhere on the board

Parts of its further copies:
C12, C14, C18, C20: 0.1uF; C_0603_1608Metric_Pad1.08x0.95mm_HandSolder
C16: 0.47uF; C_0603_1608Metric_Pad1.08x0.95mm_HandSolder
C22: 100uF; CP_Radial_D5.0mm_P2.00mm
J5: Arbor Stepper Conn; PinHeader_1x04_P2.54mm_Vertical
R2, R4: 200mΩ; C_0603_1608Metric_Pad1.08x0.95mm_HandSolder
R6: 1MΩ; C_0603_1608Metric_Pad1.08x0.95mm_HandSolder
R8: 10kΩ; C_0603_1608Metric_Pad1.08x0.95mm_HandSolder
R11: 50kΩ; C_0603_1608Metric_Pad1.08x0.95mm_HandSolder
R12: 30kΩ; C_0603_1608Metric_Pad1.08x0.95mm_HandSolder
TP6: TestPoint; TestPoint_Pad_1.0x1.0mm

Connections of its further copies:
/StepperDriver_EYE/A1_A: J5.1; also elsewhere on the board
/StepperDriver_EYE/A2_A: J5.2; also elsewhere on the board
/StepperDriver_EYE/B1_A: J5.4; also elsewhere on the board
/StepperDriver_EYE/B2_A: J5.3; also elsewhere on the board
GND: C16.2, C18.1, C20.1, C22.2, R2.2, R4.2, R12.2; also elsewhere on the board
unnamed 43: R11.2, R12.1; also elsewhere on the board
unnamed 44: C12.1; also elsewhere on the board
unnamed 45: C12.2; also elsewhere on the board
unnamed 46: R2.1; also elsewhere on the board
unnamed 47: R4.1; also elsewhere on the board
unnamed 48: C16.1, R8.2, R11.1; also elsewhere on the board
unnamed 49: C14.2, R6.1; also elsewhere on the board
unnamed 50: TP6.1; also elsewhere on the board
unnamed 51: R8.1; also elsewhere on the board
VDD: C14.1, C18.2, C20.2, C22.1, R6.2; also elsewhere on the board

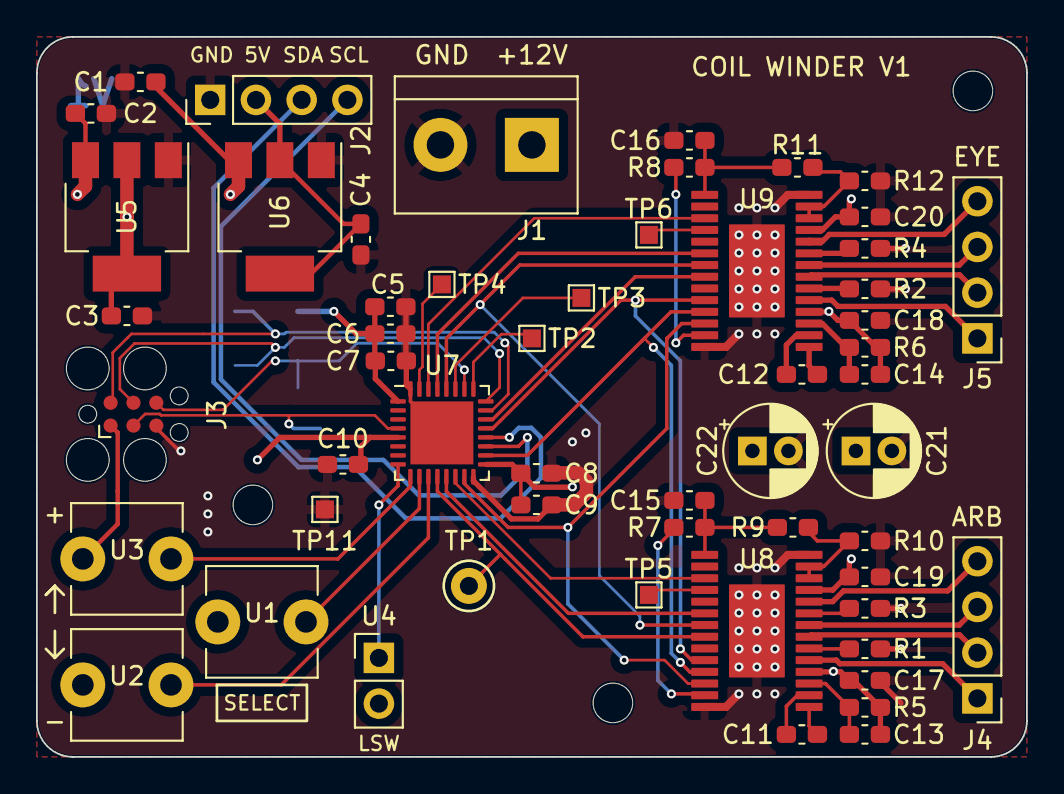
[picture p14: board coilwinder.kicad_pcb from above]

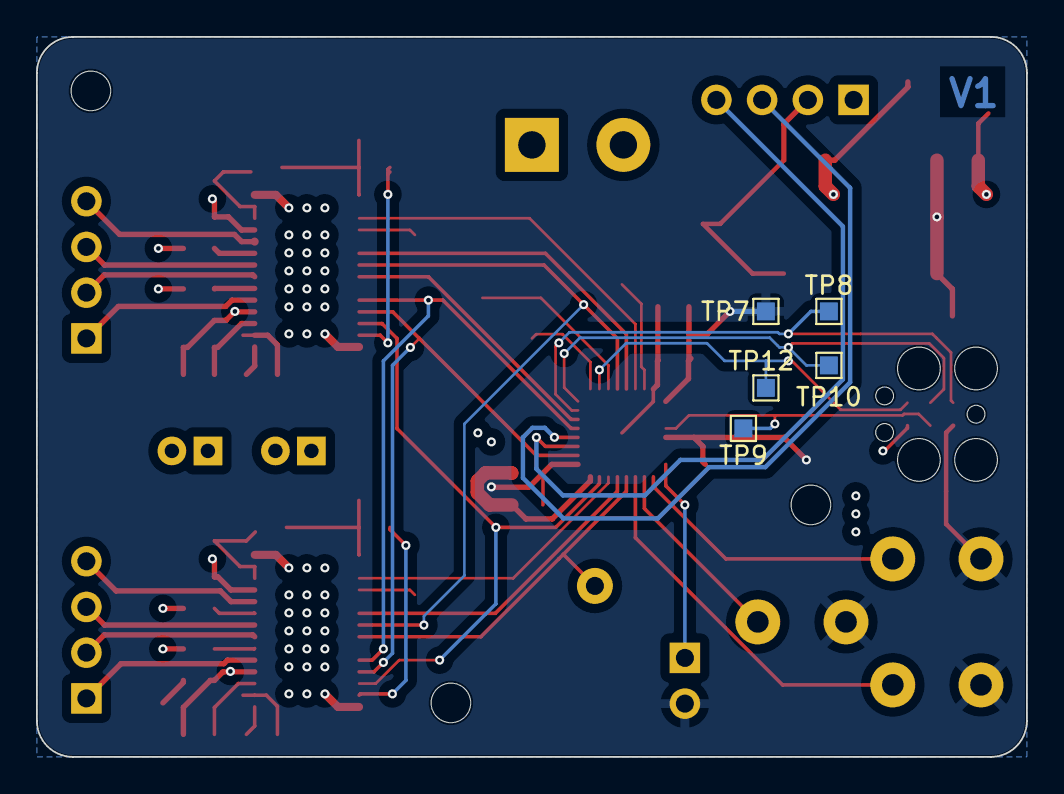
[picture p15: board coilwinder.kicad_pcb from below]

Board: 4 copper layers, 55.0 x 40.0 mm, 63 parts (5 on the bottom side), 53 nets.

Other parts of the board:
U9: HTSSOP (28) 9.70 mm × 6.40 mm; DRV8825

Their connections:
/EYE_STEPPER_DIR: U9.20 (DIR); also elsewhere on the board
/EYE_STEPPER_SLP: U9.17 (nSLEEP); also elsewhere on the board
/EYE_STEPPER_STP: U9.22 (STEP); also elsewhere on the board
/MICROSTEP_M0: U9.24 (MODE0); also elsewhere on the board
/MICROSTEP_M1: U9.25 (MODE1); also elsewhere on the board
/MICROSTEP_M2: U9.26 (MODE2); also elsewhere on the board
/STEPPER_ENABLE: U9.21 (nENBL); also elsewhere on the board
/StepperDriver_EYE/A1_A: U9.5 (AOUT1); also elsewhere on the board
/StepperDriver_EYE/A2_A: U9.7 (AOUT2); also elsewhere on the board
/StepperDriver_EYE/B1_A: U9.10 (BOUT1); also elsewhere on the board
/StepperDriver_EYE/B2_A: U9.8 (BOUT2); also elsewhere on the board
GND: U9.14 (GND2), U9.28 (GND), U9.29 (PPAD); also elsewhere on the board
unnamed 43: U9.12 (AVREF), U9.13 (BVREF); also elsewhere on the board
unnamed 44: U9.1 (CP1); also elsewhere on the board
unnamed 45: U9.2 (CP2); also elsewhere on the board
unnamed 46: U9.6 (ISENA); also elsewhere on the board
unnamed 47: U9.9 (ISENB); also elsewhere on the board
unnamed 48: U9.15 (V3P3OUT); also elsewhere on the board
unnamed 49: U9.3 (VCP); also elsewhere on the board
unnamed 50: U9.18 (nFAULT); also elsewhere on the board
unnamed 51: U9.27 (nHOME); also elsewhere on the board
VDD: U9.4 (VMA), U9.11 (VMB); also elsewhere on the board

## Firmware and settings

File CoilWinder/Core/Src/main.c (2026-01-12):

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
/* Includes ------------------------------------------------------------------*/
#include "main.h"
#include "cmsis_os.h"

I2C_HandleTypeDef hi2c1;

TIM_HandleTypeDef htim1;

/* Definitions for UITask */
osThreadId_t UITaskHandle;
const osThreadAttr_t UITask_attributes = {
  .name = "UITask",
  .stack_size = 128 * 4,
  .priority = (osPriority_t) osPriorityNormal,
};
/* Definitions for motorTask */
osThreadId_t motorTaskHandle;
const osThreadAttr_t motorTask_attributes = {
  .name = "motorTask",
  .stack_size = 128 * 4,
  .priority = (osPriority_t) osPriorityAboveNormal,
};
/* USER CODE BEGIN PV */

CoilParameters_t Coil0;
Button_t IncrementButton;
Button_t DecrementButton;
Button_t SelectButton;
UserInput_t UserInput0;

UIField_t WireField;
UIField_t DiamField;
UIField_t WidthField;
UIField_t LayersField;

UIField_t * UIFields[] = {&WireField, &DiamField, &WidthField, &LayersField};

DRV8825_Stepper_t ArborStepper;
DRV8825_Stepper_t EyeStepper;
EyeParameters_t Eye0;
ArborParameters_t Arbor0;

bool redrawUI = true;



/* USER CODE END PV */

void SystemClock_Config(void);
static void MX_GPIO_Init(void);
static void MX_I2C1_Init(void);
static void MX_TIM1_Init(void);
void StartDefaultTask(void *argument);
void StartTask02(void *argument);

/**
  * @brief  The application entry point.
  * @retval int
  */
int main(void)
{
  /* MCU Configuration--------------------------------------------------------*/

  /* Reset of all peripherals, Initializes the Flash interface and the Systick. */
  HAL_Init();

  /* USER CODE BEGIN Init */


	Coil_Init(&Coil0, 20, 5000, 100, 1);

    Button_Init(&DecrementButton, GPIOA, DEC_BTN_Pin, 1, 1);
    Button_Init(&IncrementButton, GPIOA, INC_BTN_Pin, 1, 1);
    Button_Init(&SelectButton, GPIOA, SEL_BTN_Pin, 0, 1);

    UserInput_Init(&UserInput0, &DecrementButton, &IncrementButton, &SelectButton);

    UIField_Init(	&WireField,
    					UI_1_X, UI_1_Y, UI_FIELD_OFFSET, UI_1_MULT, FIXED_POINT_PRECISION,
    					"Wire[mm]",
    					&UserInput0,
    					Coil_getWireDiam_10um, Coil_incWireDiam_10um);

    	UIField_Init(	&DiamField,
    					UI_2_X, UI_2_Y, UI_FIELD_OFFSET, UI_2_MULT, FIXED_POINT_PRECISION,
    					"Diam[mm]",
    					&UserInput0,
    					Coil_getCoilDiam_10um, Coil_incCoilDiam_10um);

    	UIField_Init(	&WidthField,
    					UI_3_X, UI_3_Y, UI_FIELD_OFFSET, UI_3_MULT, FIXED_POINT_PRECISION,
    					"Width[mm]",
    					&UserInput0,
    					Coil_getCoilWidth_10um, Coil_incCoilWidth_10um);

    	UIField_Init(	&LayersField,
    					UI_4_X, UI_4_Y, UI_FIELD_OFFSET, UI_4_MULT, 0,
    					"Layers",
    					&UserInput0,
    					Coil_getCoilLayers, Coil_incCoilLayers);

    	DRV8825_Init(	&ArborStepper,
    					GPIOA, STEPPER_ARBOR_STP_Pin,
    					GPIOA, STEPPER_A_DIR_Pin,
    					GPIOB, STEPPER_A_SLP_Pin,
    					NULL, -1,
    					NULL, -1,
    					NULL, -1,
    					NULL, -1,
    					NULL, -1, MICROSTEP_LEVEL);

    	DRV8825_Init(	&EyeStepper,
    					GPIOA, STEPPER_B_STP_Pin,
    					GPIOB, STEPPER_B_DIR_Pin,
    					GPIOB, STEPPER_B_SLP_Pin,
    					NULL, -1,
    					NULL, -1,
    					NULL, -1,
    					NULL, -1,
    					NULL, -1, MICROSTEP_LEVEL);

    	Eye_Init(&Eye0, &EyeStepper, EYE_LENGTH, 0.0, EYE_STEPS, GPIOA, LIMIT_SW_Pin);
    	Arbor_Init(&Arbor0, &ArborStepper, 100, ARBOR_STEPS);

  /* USER CODE END Init */

  /* Configure the system clock */
  SystemClock_Config();

  /* Initialize all configured peripherals */
  MX_GPIO_Init();
  MX_I2C1_Init();
  MX_TIM1_Init();
  /* Init scheduler */
  osKernelInitialize();

  /* USER CODE BEGIN RTOS_MUTEX */
    /* add mutexes, ... */
  /* USER CODE END RTOS_MUTEX */

  /* USER CODE BEGIN RTOS_SEMAPHORES */
    /* add semaphores, ... */
  /* USER CODE END RTOS_SEMAPHORES */

  /* USER CODE BEGIN RTOS_TIMERS */
    /* start timers, add new ones, ... */
  /* USER CODE END RTOS_TIMERS */

  /* USER CODE BEGIN RTOS_QUEUES */
    /* add queues, ... */
  /* USER CODE END RTOS_QUEUES */

  /* Create the thread(s) */
  /* creation of UITask */
  UITaskHandle = osThreadNew(StartDefaultTask, NULL, &UITask_attributes);

  /* creation of motorTask */
  motorTaskHandle = osThreadNew(StartTask02, NULL, &motorTask_attributes);

  /* USER CODE BEGIN RTOS_THREADS */
    /* add threads, ... */
  /* USER CODE END RTOS_THREADS */

  /* USER CODE BEGIN RTOS_EVENTS */
    /* add events, ... */
  /* USER CODE END RTOS_EVENTS */

  /* Start scheduler */
  osKernelStart();

  /* We should never get here as control is now taken by the scheduler */
  /* Infinite loop */
  /* USER CODE BEGIN WHILE */
    while (1) {
    /* USER CODE END WHILE */

    /* USER CODE BEGIN 3 */
    }
  /* USER CODE END 3 */
}

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
/* USER CODE BEGIN Header_StartDefaultTask */
/**
 * @brief  Function implementing the defaultTask thread.
 * @param  argument: Not used
 * @retval None
 */
/* USER CODE END Header_StartDefaultTask */
void StartDefaultTask(void *argument)
{
  /* USER CODE BEGIN 5 */

    unsigned int uiMaster = HALF_UINT_MAX;
    uint8_t uiControl = 0;


    HD44780_Init(4);

    HAL_Delay(1000);

	HD44780_Clear();

    /* Infinite loop */
    for (;;) {

    	if(redrawUI) {
			for(int ii = 0; ii < 4; ii++) {
				UIField_PrintTitle(UIFields[ii]);
				UIField_Print(UIFields[ii], &Coil0);
			}

			HD44780_SetCursor(UI_5_X, UI_5_Y);
            HD44780_PrintStr("~");

			redrawUI = false;
    	}



    	UserInput_Update(&UserInput0);

        uiMaster += (UserInput_Get(&UserInput0) == Select);

        uiControl = (uiMaster) % 5;



        bool field_modified = ! (UserInput_Get(&UserInput0) == Select || UserInput_Get(&UserInput0) == None);

        if (field_modified)
            HD44780_NoCursor();
        else
            HD44780_Cursor();



        switch (uiControl) {

        case 0:
        case 1:
        case 2:
        case 3:
        	UIField_SetCursorOnField(UIFields[uiControl]);
        	UIField_UpdateValue(UIFields[uiControl], &Coil0);
        	UIField_RePrint(UIFields[uiControl], &Coil0);

            break;

        case 4:
            HD44780_SetCursor(UI_5_X, UI_5_Y);

            if (field_modified && Coil_isValid(&Coil0))
            	vTaskResume(motorTaskHandle);

            break;

        }

        osDelay(10);

    }
  /* USER CODE END 5 */
}

/* USER CODE BEGIN Header_StartTask02 */
/**
 * @brief Function implementing the motorTask thread.
 * @param argument: Not used
 * @retval None
 */
/* USER CODE END Header_StartTask02 */
void StartTask02(void *argument)
{
  /* USER CODE BEGIN StartTask02 */


	int nCoils, nLayers;
	char str[20];





	vTaskSuspend(motorTaskHandle);


    /* Infinite loop */
    for (;;) {

        	HD44780_Clear();

            nCoils = Coil_getCoilWidth_10um(&Coil0) /  Coil_getWireDiam_10um(&Coil0);
            nLayers = Coil_getCoilLayers(&Coil0);

            Arbor_Start(&Arbor0);
            Eye_Start(&Eye0);

            HAL_Delay(3000);
            HD44780_PrintTitle("Homing E Axis...", 0);

            if(Eye_FindHome(&Eye0) == 0) {


            	HD44780_PrintTitle("Set Arbor Position", 0);
            	HD44780_PrintTitle("[SELECT] to cont.", 1);

                while (UserInput_Get(&UserInput0) != Select);

            	HD44780_Clear();
            	HD44780_PrintTitle("Winding coil...", 0);

				//Coil winding starts here
				for (int layersWound = 0; layersWound < nLayers; layersWound++) {

					//alternate the direction of the winding with each layer
					int dir = (-1 * (layersWound % 2)) | ((layersWound+1) % 2);

					//Once a layer of coils has been wound, advance the eye a half coil distance
					//too ensure that the next layer is wound in the root of the previous layer
					if(layersWound)
						Eye_MoveWireDiameters(&Eye0, &Coil0, 0.5*dir);


					//Each iteration winds a single wrap of coil
					for (int coilsWound = 0; coilsWound < nCoils; coilsWound++) {

						//Print percent completion
		                sprintf(str, "%d", (100*(layersWound * nCoils + coilsWound)) / (nLayers * nCoils));
		                strcat(str, "% Complete");
		                HD44780_PrintTitle(str, 1);

		                //odd bug, initializes GPIO pins for some reason, need to fix
						GPIOB->BRR = (uint32_t)STEPPER_ARBOR_STP_Pin;
						GPIOB->BRR = (uint32_t)STEPPER_B_STP_Pin;

						Arbor_SingleRevolution(&Arbor0, &Coil0);
						Eye_MoveWireDiameters(&Eye0, &Coil0, 1*dir);

					}
				}

            } else {
                HD44780_Clear();
            	HD44780_PrintTitle("Homing Failed :(", 0);
            }

            Arbor_End(&Arbor0);
            Eye_End(&Eye0);
            redrawUI = true;
            vTaskSuspend(motorTaskHandle);
    }
  /* USER CODE END StartTask02 */
}

/**
  * @brief  This function is executed in case of error occurrence.
  * @retval None
  */
void Error_Handler(void)
{
  /* USER CODE BEGIN Error_Handler_Debug */
    /* User can add his own implementation to report the HAL error return state */
    __disable_irq();
    while (1) {}
  /* USER CODE END Error_Handler_Debug */
}

#ifdef  USE_FULL_ASSERT
/**
  * @brief  Reports the name of the source file and the source line number
  *         where the assert_param error has occurred.
  * @param  file: pointer to the source file name
  * @param  line: assert_param error line source number
  * @retval None
  */
void assert_failed(uint8_t *file, uint32_t line)
{
  /* USER CODE BEGIN 6 */
    /* User can add his own implementation to report the file name and line number,
       ex: printf("Wrong parameters value: file %s on line %d\r\n", file, line) */
  /* USER CODE END 6 */
}
#endif /* USE_FULL_ASSERT */

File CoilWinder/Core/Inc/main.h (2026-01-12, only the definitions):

#define LIMIT_SW_Pin GPIO_PIN_2
#define LIMIT_SW_GPIO_Port GPIOA
#define INC_BTN_Pin GPIO_PIN_3
#define INC_BTN_GPIO_Port GPIOA
#define SEL_BTN_Pin GPIO_PIN_4
#define SEL_BTN_GPIO_Port GPIOA
#define DEC_BTN_Pin GPIO_PIN_5
#define DEC_BTN_GPIO_Port GPIOA
#define STEPPER_ARBOR_STP_Pin GPIO_PIN_6
#define STEPPER_ARBOR_STP_GPIO_Port GPIOA
#define STEPPER_A_DIR_Pin GPIO_PIN_7
#define STEPPER_A_DIR_GPIO_Port GPIOA
#define STEPPER_A_SLP_Pin GPIO_PIN_0
#define STEPPER_A_SLP_GPIO_Port GPIOB
#define MICROSTEP_M2_Pin GPIO_PIN_1
#define MICROSTEP_M2_GPIO_Port GPIOB
#define MICROSTEP_M1_Pin GPIO_PIN_8
#define MICROSTEP_M1_GPIO_Port GPIOA
#define MICROSTEP_M0_Pin GPIO_PIN_11
#define MICROSTEP_M0_GPIO_Port GPIOA
#define STEPPER_B_STP_Pin GPIO_PIN_12
#define STEPPER_B_STP_GPIO_Port GPIOA
#define STEPPER_ENABLE_Pin GPIO_PIN_5
#define STEPPER_ENABLE_GPIO_Port GPIOB
#define STEPPER_B_DIR_Pin GPIO_PIN_6
#define STEPPER_B_DIR_GPIO_Port GPIOB
#define STEPPER_B_SLP_Pin GPIO_PIN_7
#define STEPPER_B_SLP_GPIO_Port GPIOB

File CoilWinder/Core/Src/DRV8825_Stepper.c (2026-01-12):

/*
 * DRV8825_Stepper.c
 *
 *  Created on: Aug 11, 2023
 *      Author: andre
 */

#include "DRV8825_Stepper.h"
#include "stm32l4xx_hal.h"
#include "CoilWinderUtils.h"

// Private Helper Functions

void DRV8825_setMicroStepDirect(DRV8825_Stepper_t* driver, uint8_t M0, uint8_t M1, uint8_t M2) {
	HAL_GPIO_WritePin(driver->MICROSTEP_Pin_M0_Port, driver->MICROSTEP_Pin_M0, M0);
	HAL_GPIO_WritePin(driver->MICROSTEP_Pin_M1_Port, driver->MICROSTEP_Pin_M1, M1);
	HAL_GPIO_WritePin(driver->MICROSTEP_Pin_M2_Port, driver->MICROSTEP_Pin_M2, M2);
}

uint8_t DRV8825_microsteppingPinsNotConfigured(DRV8825_Stepper_t* driver) {
	if(	driver->MICROSTEP_Pin_M0_Port == NULL || driver->MICROSTEP_Pin_M0 == -1 ||
		driver->MICROSTEP_Pin_M1_Port == NULL || driver->MICROSTEP_Pin_M1 == -1 ||
		driver->MICROSTEP_Pin_M2_Port == NULL || driver->MICROSTEP_Pin_M2 == -1)
			return 1;

	return 0;
}


// Public Driver Functions

int DRV8825_Init(	DRV8825_Stepper_t* driver,
					GPIO_TypeDef* STEP_Pin_Port,
					uint16_t STEP_Pin,
					GPIO_TypeDef* DIR_Pin_Port,
					uint16_t DIR_Pin,
					GPIO_TypeDef* SLEEP_Pin_Port,
					uint16_t SLEEP_Pin,
					GPIO_TypeDef* RESET_Pin_Port,
					uint16_t RESET_Pin,
					GPIO_TypeDef* ENABLE_Pin_Port,
					uint16_t ENABLE_Pin,
					GPIO_TypeDef* MICROSTEP_Pin_M0_Port,
					uint16_t MICROSTEP_Pin_M0,
					GPIO_TypeDef* MICROSTEP_Pin_M1_Port,
					uint16_t MICROSTEP_Pin_M1,
					GPIO_TypeDef* MICROSTEP_Pin_M2_Port,
					uint16_t MICROSTEP_Pin_M2,
					uint8_t microstep_config  ) {


	if(STEP_Pin_Port == NULL || STEP_Pin == -1)
		return -1;

	driver->STEP_Pin_Port = STEP_Pin_Port;
	driver->STEP_Pin = STEP_Pin;

	driver->DIR_Pin_Port = DIR_Pin_Port;
	driver->DIR_Pin = DIR_Pin;

	driver->SLEEP_Pin_Port = SLEEP_Pin_Port;
	driver->SLEEP_Pin = SLEEP_Pin;

	driver->RESET_Pin_Port = RESET_Pin_Port;
	driver->RESET_Pin = RESET_Pin;

	driver->ENABLE_Pin_Port = ENABLE_Pin_Port;
	driver->ENABLE_Pin = ENABLE_Pin;

	driver->MICROSTEP_Pin_M0_Port = MICROSTEP_Pin_M0_Port;
	driver->MICROSTEP_Pin_M0 = MICROSTEP_Pin_M0;

	driver->MICROSTEP_Pin_M1_Port = MICROSTEP_Pin_M1_Port;
	driver->MICROSTEP_Pin_M1 = MICROSTEP_Pin_M1;

	driver->MICROSTEP_Pin_M2_Port = MICROSTEP_Pin_M2_Port;
	driver->MICROSTEP_Pin_M2 = MICROSTEP_Pin_M2;

	DRV8825_SetMicrostepLevel(driver, microstep_config);
	DRV8825_Enable(driver);
	DRV8825_Sleep(driver);
	DRV8825_SetDirection(driver, 0);

	HAL_GPIO_WritePin(driver->DIR_Pin_Port, driver->DIR_Pin, 1);

	return 0;

}


int DRV8825_GetDirection(DRV8825_Stepper_t* driver) {
	if(driver->DIR_Pin_Port == NULL || driver->DIR_Pin == -1)
		return -1;

	return HAL_GPIO_ReadPin(driver->DIR_Pin_Port, driver->DIR_Pin);
}

int DRV8825_SetDirection(DRV8825_Stepper_t* driver, uint8_t dir) {
	if(driver->DIR_Pin_Port == NULL || driver->DIR_Pin == -1)
		return -1;

	dir = !!dir;

	HAL_GPIO_WritePin(driver->DIR_Pin_Port, driver->DIR_Pin, dir);

	return 0;
}

int DRV8825_ToggleDirection(DRV8825_Stepper_t* driver) {
	if(driver->DIR_Pin_Port == NULL || driver->DIR_Pin == -1)
		return -1;

	uint8_t dir = HAL_GPIO_ReadPin(driver->DIR_Pin_Port, driver->DIR_Pin);

	HAL_GPIO_WritePin(driver->DIR_Pin_Port, driver->DIR_Pin, !dir);

	return 0;
}

void DRV8825_Step(DRV8825_Stepper_t* driver, uint32_t delay_millis) {

	HAL_GPIO_WritePin(driver->STEP_Pin_Port, driver->STEP_Pin, 0);
	HAL_GPIO_WritePin(driver->STEP_Pin_Port, driver->STEP_Pin, 1);
	HAL_Delay(delay_millis);

}
void DRV8825_QuickStep(DRV8825_Stepper_t* driver, uint32_t iters)
{
	HAL_GPIO_WritePin(driver->STEP_Pin_Port, driver->STEP_Pin, 0);
	delay_iterations(iters);
	HAL_GPIO_WritePin(driver->STEP_Pin_Port, driver->STEP_Pin, 1);
	delay_iterations(iters);

}
int DRV8825_Wake(DRV8825_Stepper_t* driver) {
	if(driver->SLEEP_Pin_Port == NULL || driver->SLEEP_Pin == -1)
		return -1;

	HAL_GPIO_WritePin(driver->SLEEP_Pin_Port, driver->SLEEP_Pin, 1);

	return 0;
}

int DRV8825_Sleep(DRV8825_Stepper_t* driver) {
	if(driver->SLEEP_Pin_Port == NULL || driver->SLEEP_Pin == -1)
		return -1;
	
	HAL_GPIO_WritePin(driver->SLEEP_Pin_Port, driver->SLEEP_Pin, 0);
	
	return 0;
}

int DRV8825_Enable(DRV8825_Stepper_t* driver) {
	if(driver->ENABLE_Pin_Port == NULL || driver->ENABLE_Pin == -1)
		return -1;
	
	HAL_GPIO_WritePin(driver->ENABLE_Pin_Port, driver->ENABLE_Pin, 0);
	
	return 0;
}


int DRV8825_Disable(DRV8825_Stepper_t* driver) {
	if(driver->ENABLE_Pin_Port == NULL || driver->ENABLE_Pin == -1)
		return -1;
	
	HAL_GPIO_WritePin(driver->ENABLE_Pin_Port, driver->ENABLE_Pin, 1);
	
	return 0;
}


int DRV8825_Reset(DRV8825_Stepper_t* driver) {
	if(driver->RESET_Pin_Port == NULL || driver->RESET_Pin == -1)
		return -1;

	HAL_GPIO_WritePin(driver->RESET_Pin_Port, driver->RESET_Pin, 0);
	HAL_Delay(100);
	HAL_GPIO_WritePin(driver->RESET_Pin_Port, driver->RESET_Pin, 1);

	return 0;
}



int DRV8825_SetMicrostepLevel(DRV8825_Stepper_t* driver, uint8_t microstep_level) {

	if(DRV8825_microsteppingPinsNotConfigured(driver))
		return -1;

	uint8_t status;

	switch(microstep_level) {

	case 1:
		DRV8825_setMicroStepDirect(driver, 0, 0, 0);
		status = 0;
		break;
	case 2:
		DRV8825_setMicroStepDirect(driver, 1, 0, 0);
		status = 0;
		break;
	case 4:
		DRV8825_setMicroStepDirect(driver, 0, 1, 0);
		status = 0;
		break;
	case 8:
		DRV8825_setMicroStepDirect(driver, 1, 1, 0);
		status = 0;
		break;
	case 16:
		DRV8825_setMicroStepDirect(driver, 0, 0, 1);
		status = 0;
		break;
	case 32:
		DRV8825_setMicroStepDirect(driver, 1, 1, 1);
		status = 0;
		break;
	default:
		status = 1;
	}

	if(status == 0)
		driver->microstep_config = microstep_level;

	return status;
}

int DRV8825_GetMicrostepLevel(DRV8825_Stepper_t* driver) {
	if(DRV8825_microsteppingPinsNotConfigured(driver))
		return -1;

	return driver->microstep_config;
}

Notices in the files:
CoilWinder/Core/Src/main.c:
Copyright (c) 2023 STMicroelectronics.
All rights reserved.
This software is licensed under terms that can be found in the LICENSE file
